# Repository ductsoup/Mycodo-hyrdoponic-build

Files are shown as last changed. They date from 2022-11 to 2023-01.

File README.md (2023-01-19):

# Mycodo-hyrdoponic-build
A straightforward example of a hardware build to run Mycodo for hydroponics.

## Overview
A few years ago we moved and I finally had the space to start messing around with indoor hydroponics to grow fresh food in winter. At first I used the Kratky method because it was cheap, easy and simple. It worked very well but had it's limitations. As things grew they required more and more tending, sometimes I didn't have the time necessary to take care of them properly. This season I wanted to move on to a more advanced ebb and flow setup that could support fruiting crops such as tomatoes.

Part of my day job is designing and building industrial control and building automation systems. Mechanical timers and checking water quality with handheld devices absolutely works but seemed a little low-tech. What I wanted was something easy to assemble with common tools that I could monitor remotely. This is what I wanted to measure and control:

- Water Quality
  - Temperature
  - pH
  - EC (electrical conductivity)
  - DO (dissolved oxygen)
- Air Quality
  - Temperature
  - Humidity
  - CO2
  - Vapor Pressure Deficit (calculated)
- Control
  - Pump 1 - Ebb and Flow (120VAC)
  - Pump 2 - Recirculation (120VAC)
  - Grow Light 1 (120VAC)
  - Grow Light 2 (120VAC)
  - Spare 120VAC or 24VDC relays

## Hardware
All sensors use the I2C bus. Additional I2C devices can be daisy chained.
- Raspberry Pi 3 or 4 (or equivalent)
  - [SanDisk 128GB Ultra microSDXC UHS-I Memory Card (or equivalent)](https://smile.amazon.com/gp/product/B08GYKNCCP/ref=ppx_yo_dt_b_asin_title_o04_s00?ie=UTF8&psc=1)
  - [2.5mm Nylon Standoffs (as needed)](https://smile.amazon.com/Generic-Spacer-Assorted-Raspberry-Pi-Standoff/dp/B014J1ZLD6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)
  - [GeeekPi 2x20 40 Pin Stacking Female Header Kit (as needed)](https://smile.amazon.com/dp/B08GC18NMK?psc=1&ref=ppx_yo2ov_dt_b_product_details)
- [Atlas/Whitebox Tentacle T3](https://atlas-scientific.com/electrical-isolation/whitebox-t3/)
  - [Atlas EZO™ pH Circuit and probe](https://atlas-scientific.com/embedded-solutions/ezo-ph-circuit)
  - [Atlas EZO™ Conductivity Circuit and probe](https://atlas-scientific.com/embedded-solutions/ezo-conductivity-circuit)
  - [Atlas EZO™ RTD Temperature Circuit and probe](https://atlas-scientific.com/embedded-solutions/ezo-rtd-temperature-circuit)
  - [Atlas EZO™ Dissolved Oxygen Circuit and probe (optional)](https://atlas-scientific.com/embedded-solutions/ezo-dissolved-oxygen-circuit/)
- [SCD41 CO2 Sensor Photoacoustic CO2, Temp & Humidity](http://adafru.it/5190)
  - [STEMMA QT / Qwiic JST SH 4-Pin Cable (modified)](https://www.adafruit.com/product/4399)
    - [Crimping Tool, housings, pins/sockets](https://www.pololu.com/product/1928)
- [Sequent Stackable 8-Channel Relay](https://smile.amazon.com/dp/B07KRKS67G?psc=1&ref=ppx_yo2ov_dt_b_product_details)
  - 120VAC/4A or 24VDC/4A 
  - [Cable Matters 2-Pack 16 AWG Heavy Duty Power Extension Cord 3 ft (modified)](https://smile.amazon.com/gp/product/B0153T1KNS/ref=ppx_yo_dt_b_asin_title_o01_s01?ie=UTF8&psc=1)
    - Wire Stripper/Cutter
  - [Wago 5-Wire Connectors](https://www.adafruit.com/product/874)

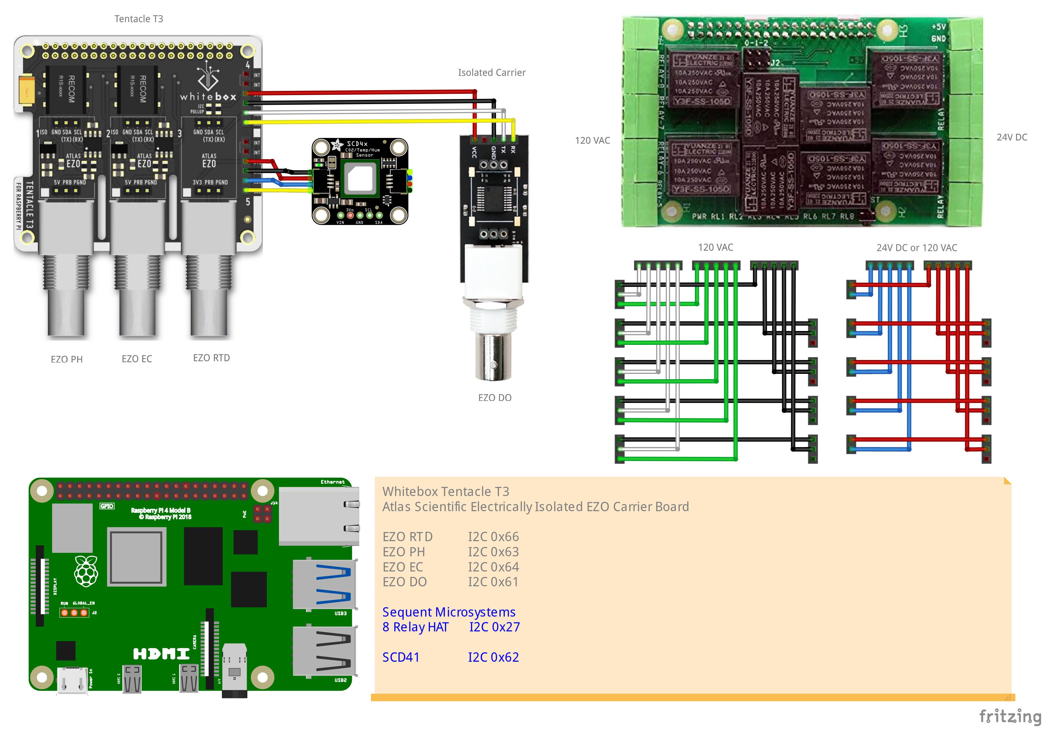
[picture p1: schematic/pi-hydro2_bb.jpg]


## Construction
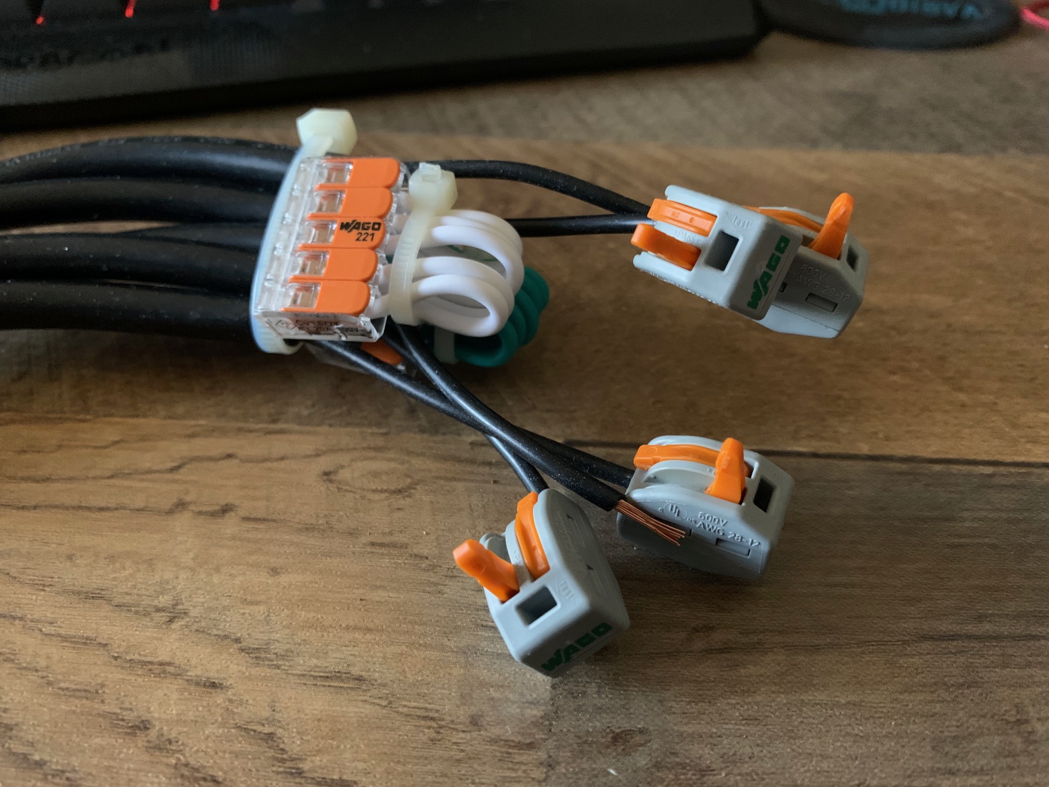
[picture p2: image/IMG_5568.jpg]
|  | For the 120VAC and 24DC use 3' (or whatever length you find convenient) extension cords with either the plug or socket removed at one end. Join using Wago connectors. Be sure to use cords and wire that can comfortably carry the load of your devices. |
| -- | :--- |
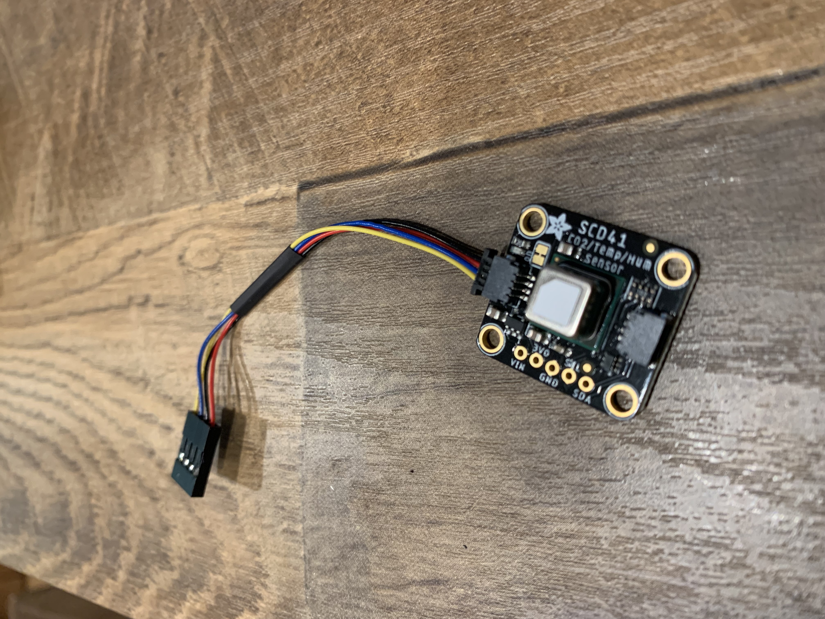
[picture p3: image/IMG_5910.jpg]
|  | The Tentacle T3 provides two spare I2C ports. To connect to SCD41 remove one end of the STEMMA QT cable and replace it with suitable 0.1" connector. Be sure to get Vin, GND, SDC and SDA in the right order. Do the same for the EZO DO board but in this case you'll make up 0.1" connections on both sides of the cable. |

## Enclosure
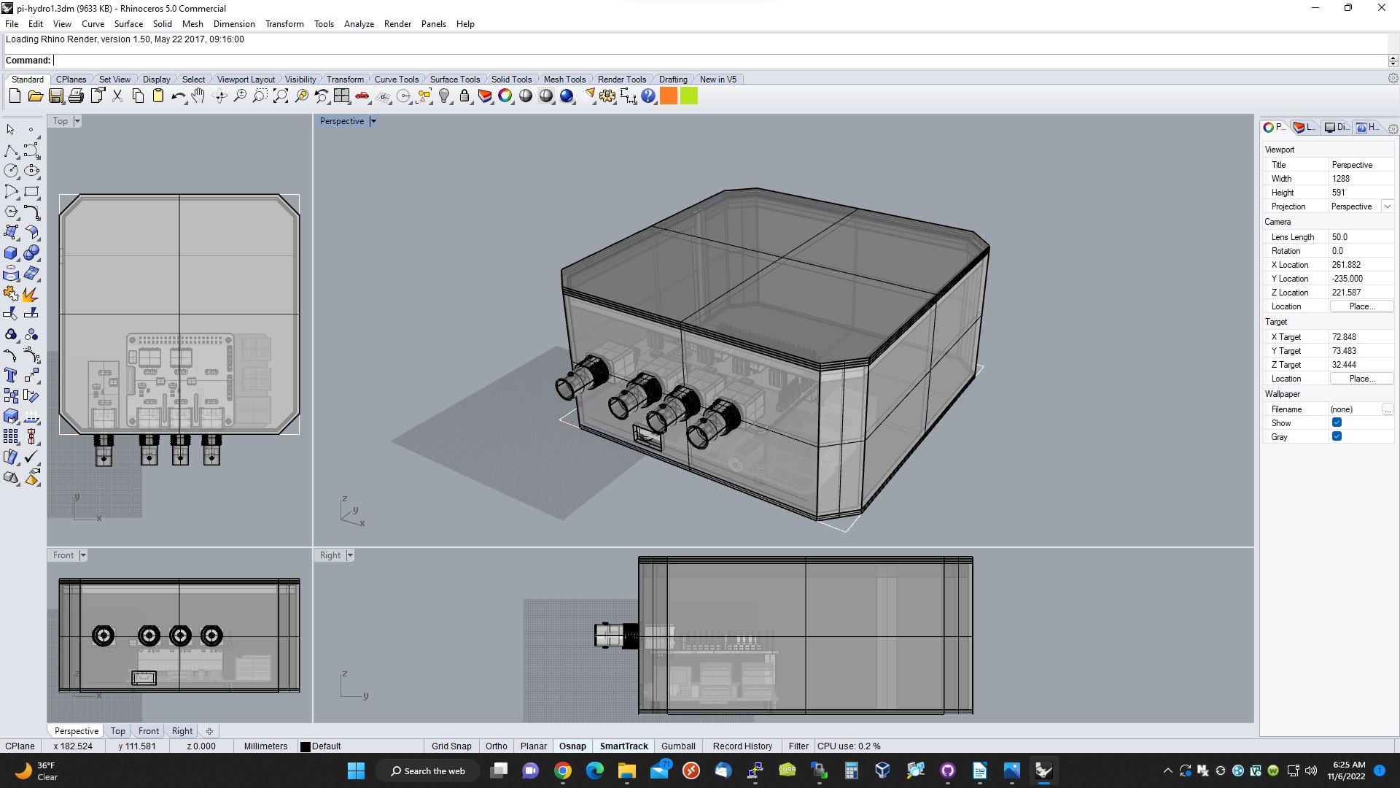
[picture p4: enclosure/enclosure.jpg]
|  | Cutouts for the BNC connectors, cords and cables require very precise measurements and special tools. Rather than modify a stock enclosure I designed and 3D printed one. Just about any material will work, I used PLA. If you're using a Pi4 or are stacking more relay boards you will have to modify the geometry. This enclosure prints on a small format Lulzbot Mini. |
| -- | :--- |

## Software
Originally I'd written my own software in Python. Then I came across [Mycodo](https://github.com/kizniche/Mycodo) which has a much nicer and more capable interface so I decided to use that instead.

Support for the Atlas and SCD41 sensors is native in Mycodo. Support for the Sequent relay board is not but fortunately there's a provision. To connect the relay board to Mycodo you'll need to install the drivers and add a shell script.

### Enable I2C
```
sudo apt update & sudo apt upgrade -y
sudo apt install -y build-essential python3-pip python3-dev python3-smbus i2c-tools
sudo raspi-config nonint do_i2c 0
sudo reboot
sudo i2cdetect -y 1

     0  1  2  3  4  5  6  7  8  9  a  b  c  d  e  f
00:                         -- -- -- -- -- -- -- -- 
10: -- -- -- -- -- -- -- -- -- -- -- -- -- -- -- -- 
20: -- -- -- -- -- -- -- 27 -- -- -- -- -- -- -- -- 
30: -- -- -- -- -- -- -- -- -- -- -- -- -- -- -- -- 
40: -- -- -- -- -- -- -- -- -- -- -- -- -- -- -- -- 
50: -- -- -- -- -- -- -- -- -- -- -- -- -- -- -- -- 
60: -- -- 62 63 64 -- 66 -- -- -- -- -- -- -- -- -- 
70: -- -- -- -- -- -- -- --  
```

### Install the Relay
```
sudo apt install git -y
# https://github.com/SequentMicrosystems/8relind-rpi/tree/main/python 
git clone https://github.com/SequentMicrosystems/8relind-rpi.git
cd 8relind-rpi/python/8relind/
sudo python3 setup.py install
cd ~/8relind-rpi/
sudo make install
8relind -h
8relind 0 test
cd ~

echo '8relind 0 write $1 $2' >script_on_off.sh
chmod +x script_on_off.sh
```
From there you can create a Shell On/Off Output in Mycodo like `/home/pi/script_on_off.sh 1 on`.

### Install the Atlas Utilities
Mycodo supports calibration for Atlas sensors. In some cases you'll want to use the Atlas utilities instead. For example, if you're using a K 0.1 or K 10 EC probe for some reason, you'll have to specify that with the Atlas utilities.
```
git clone https://github.com/AtlasScientific/Raspberry-Pi-sample-code.git
python3 Raspberry-Pi-sample-code/i2c.py
```
If you are using a Pi4 you may have problems using the Atlas utilities. A workaround for Pi 4 is [here](https://github.com/AtlasScientific/Raspberry-Pi-sample-code/issues/9).

## Gallery
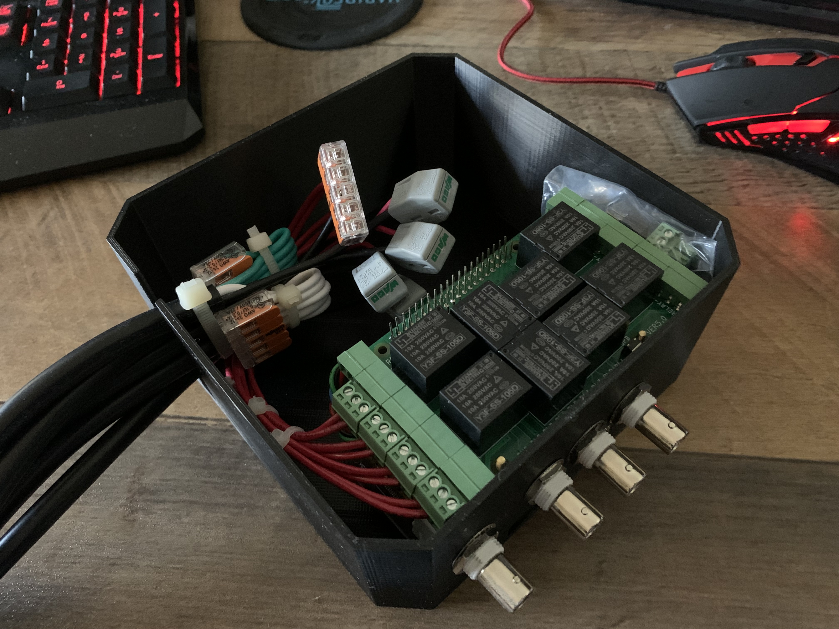
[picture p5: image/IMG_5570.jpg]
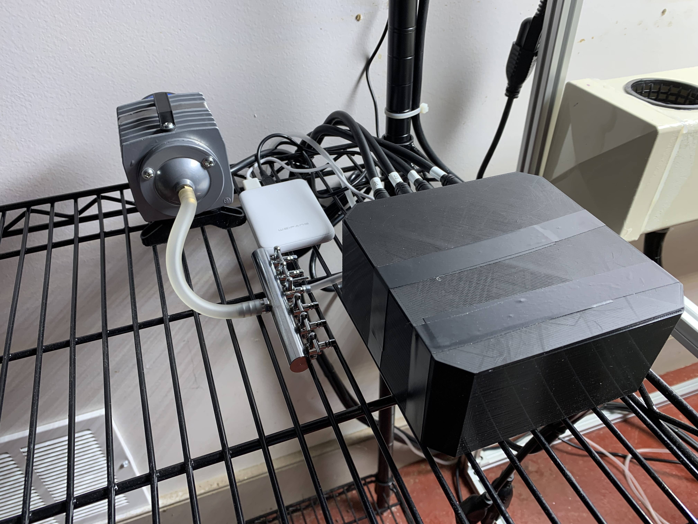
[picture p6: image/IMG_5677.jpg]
|  |   |
| --- | --- |
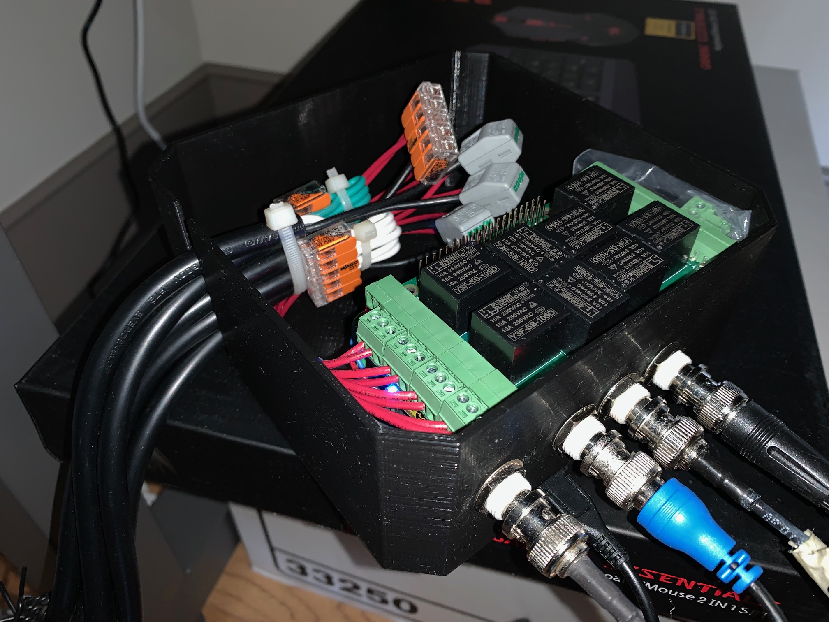
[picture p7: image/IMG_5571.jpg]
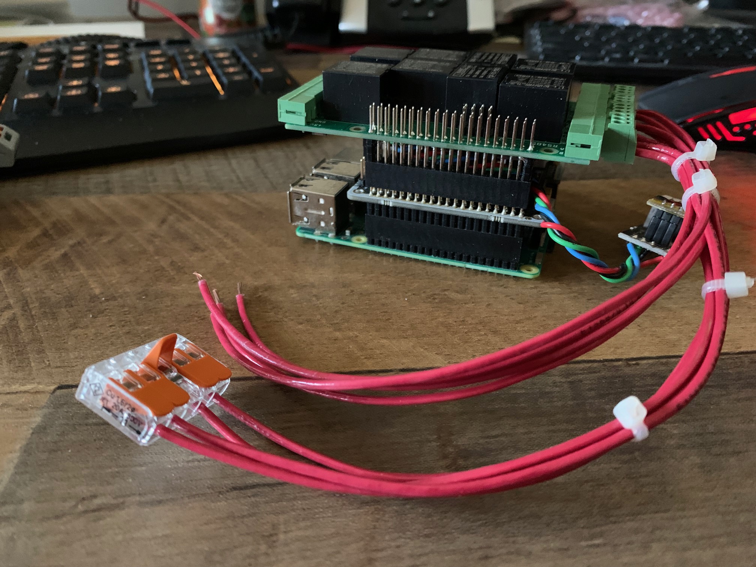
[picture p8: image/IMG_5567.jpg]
|  |  |
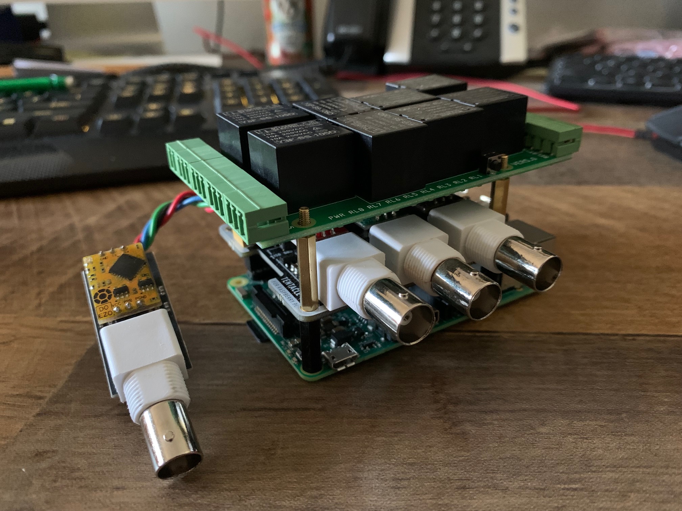
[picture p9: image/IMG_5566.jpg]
|  |  |
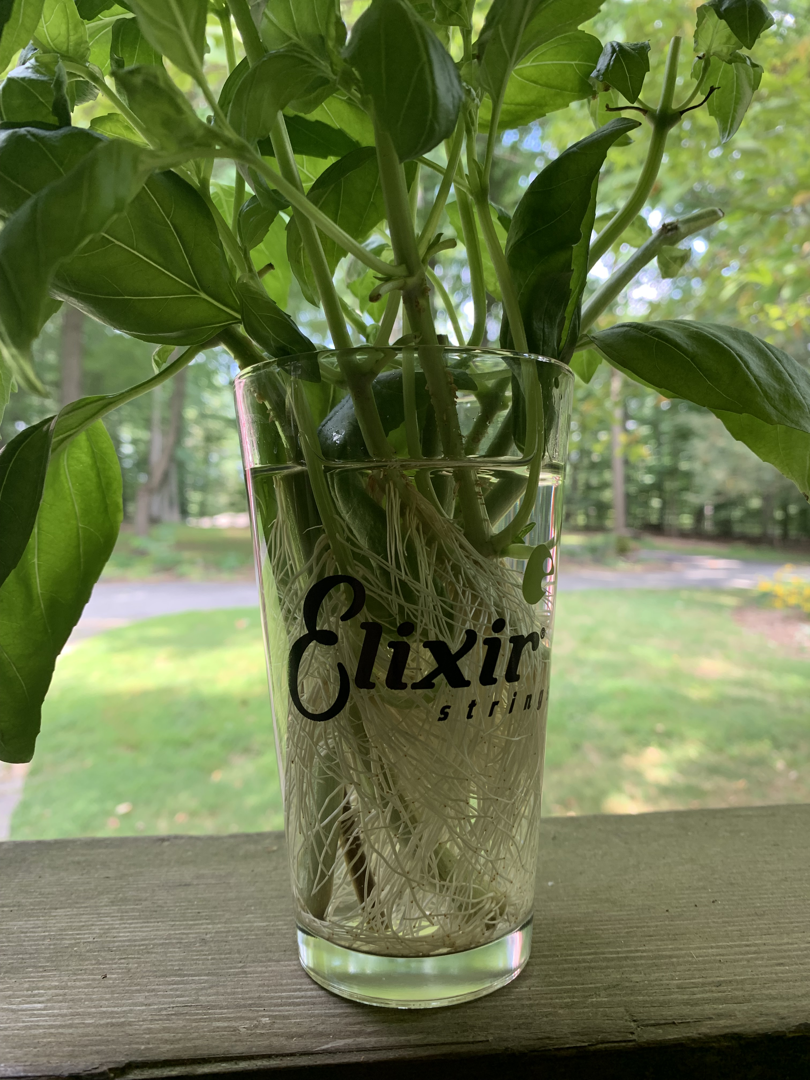
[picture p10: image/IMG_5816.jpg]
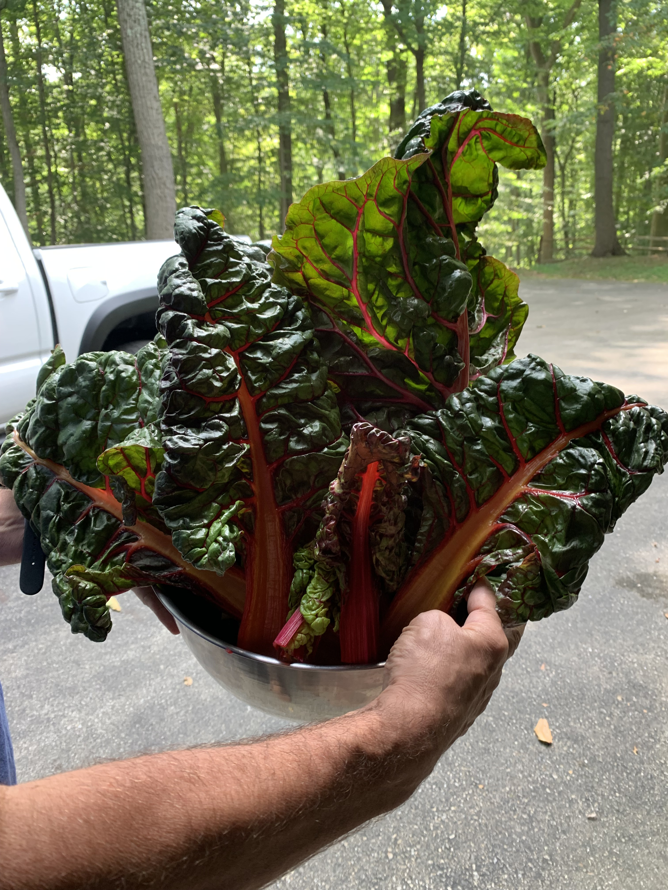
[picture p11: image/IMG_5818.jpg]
|  |  |
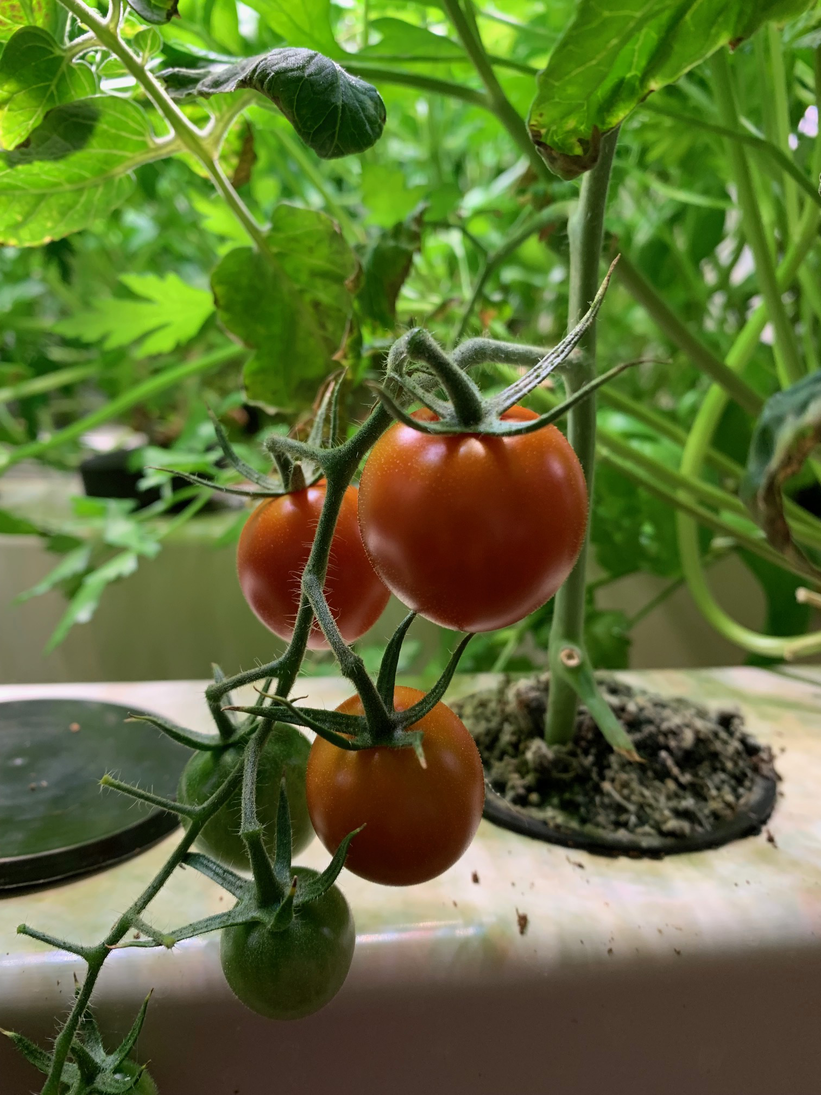
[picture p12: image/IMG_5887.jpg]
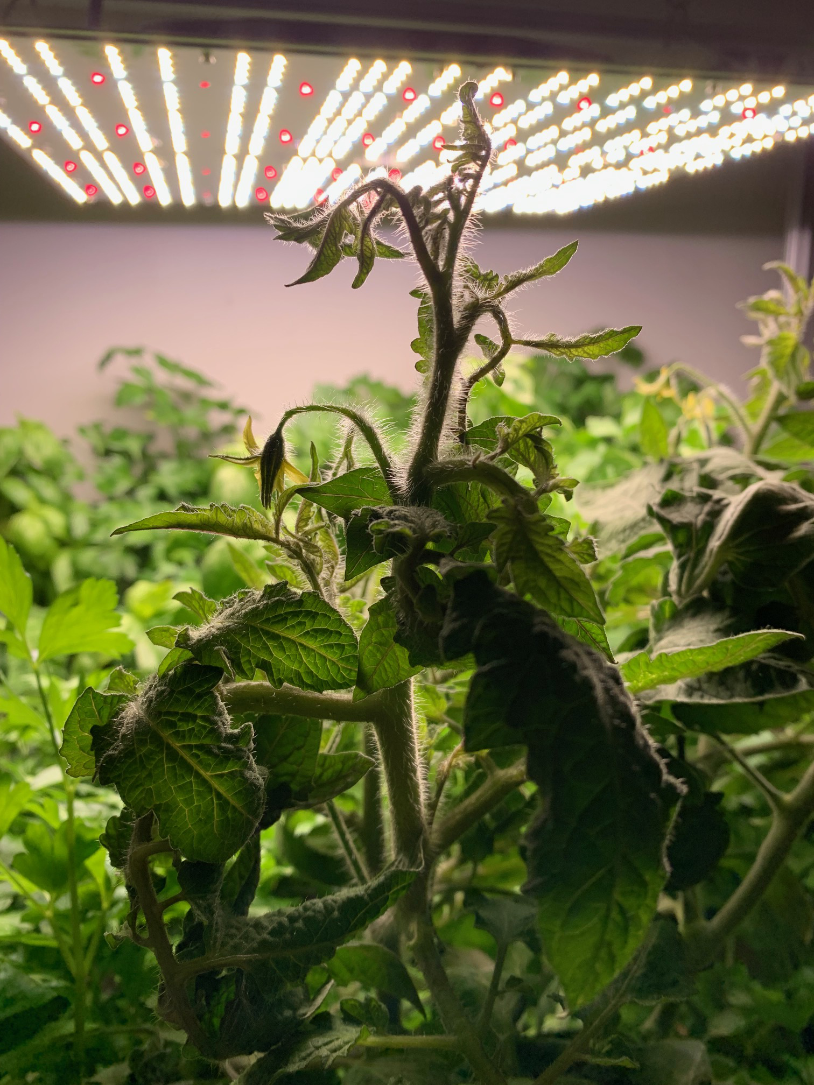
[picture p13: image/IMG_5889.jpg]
|  |  |

## Conclusion
The Pi3 works fine but it's slow. A Pi4 works much better with the caveat you need to figure a way to manage the heat it generates. Unless you're doing aquaponics the DO sensor probably isn't much use and can be elimined. The air temperature, humidity and CO2 sensor is very handy.

Just for fun I've also included a rough sketch of the frame I'm using for this system. When it came time to build that part I considered using t-slotted aluminum frames rather than a standard wire shelf from Uline. Comparing the prices for both, it was a wash so I oped for the more flexible t-slotted design. I've used extruded aluminum many times before from various vendors. Experience is Automation Direct is cheaper and faster than others.

- [Automation Direct T-Slotted Rails and Components](https://www.automationdirect.com/adc/overview/catalog/structural_frames_-z-_rails)

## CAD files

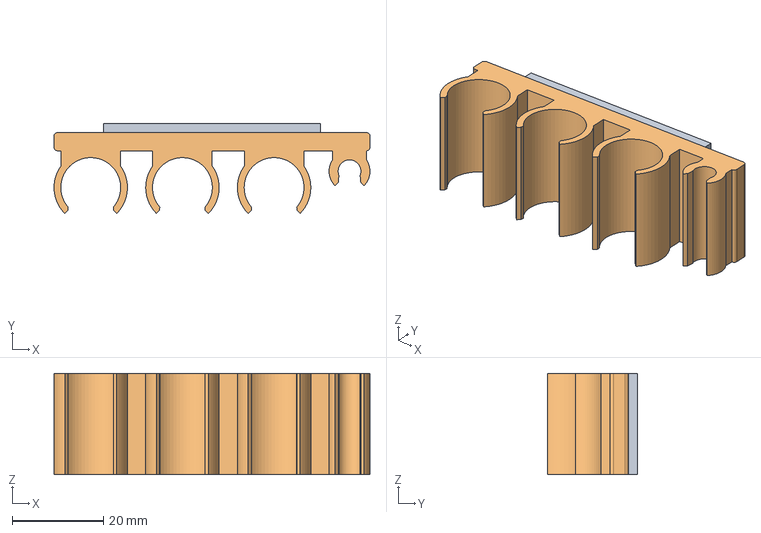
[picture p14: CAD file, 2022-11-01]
enclosure/probe_holder.stp
69.4 x 19.8 x 22.2 mm

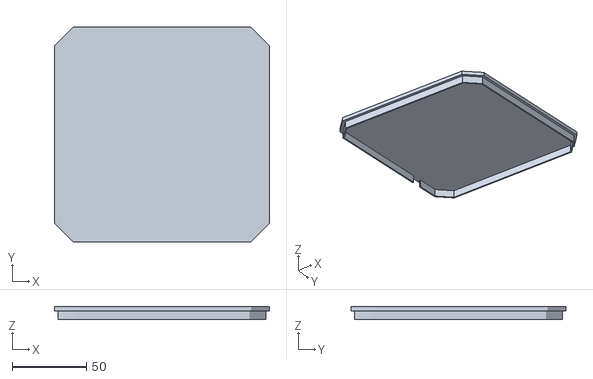
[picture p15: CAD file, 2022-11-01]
enclosure/pi-hydro1_top.stl
145.0 x 145.0 x 9.00

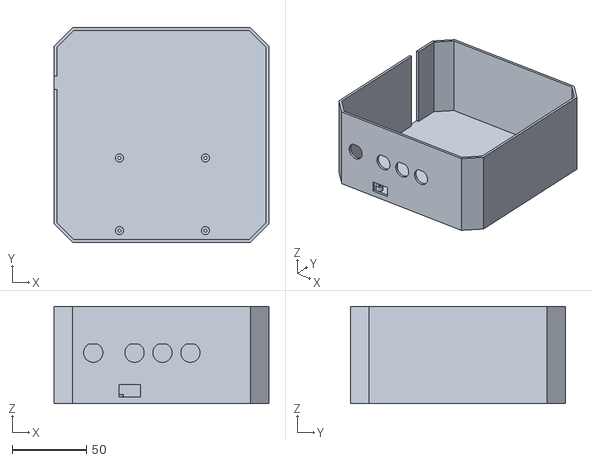
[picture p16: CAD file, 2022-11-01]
enclosure/pi-hydro1_bottom.stl
145.0 x 145.0 x 65.5

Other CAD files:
enclosure/probe_holder.3dm
enclosure/probe_holder.stl

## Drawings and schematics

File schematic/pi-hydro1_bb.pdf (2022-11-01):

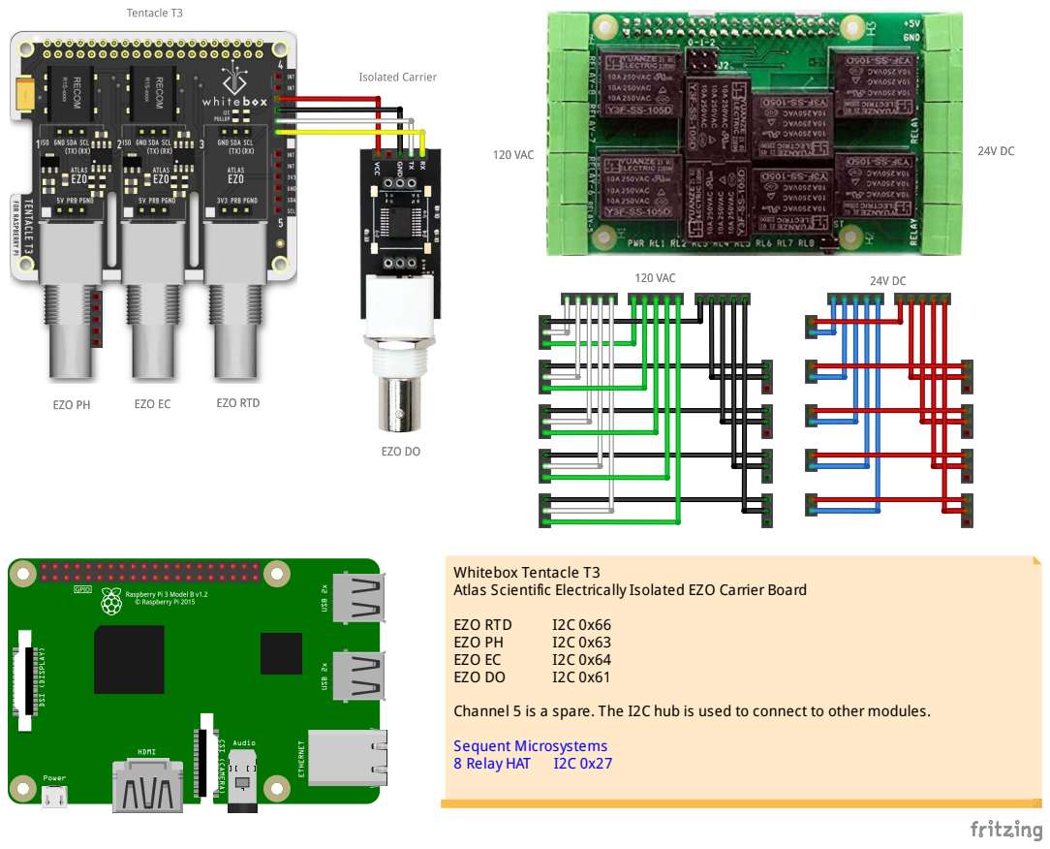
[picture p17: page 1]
EZO RTD; EZO PH; EZO EC; EZO DO; Sequent Microsystems; 8 Relay HAT

Whitebox Tentacle T3
Atlas Scientific Electrically Isolated EZO Carrier Board

Channel 5 is a spare. The I2C hub is used to connect to other modules.

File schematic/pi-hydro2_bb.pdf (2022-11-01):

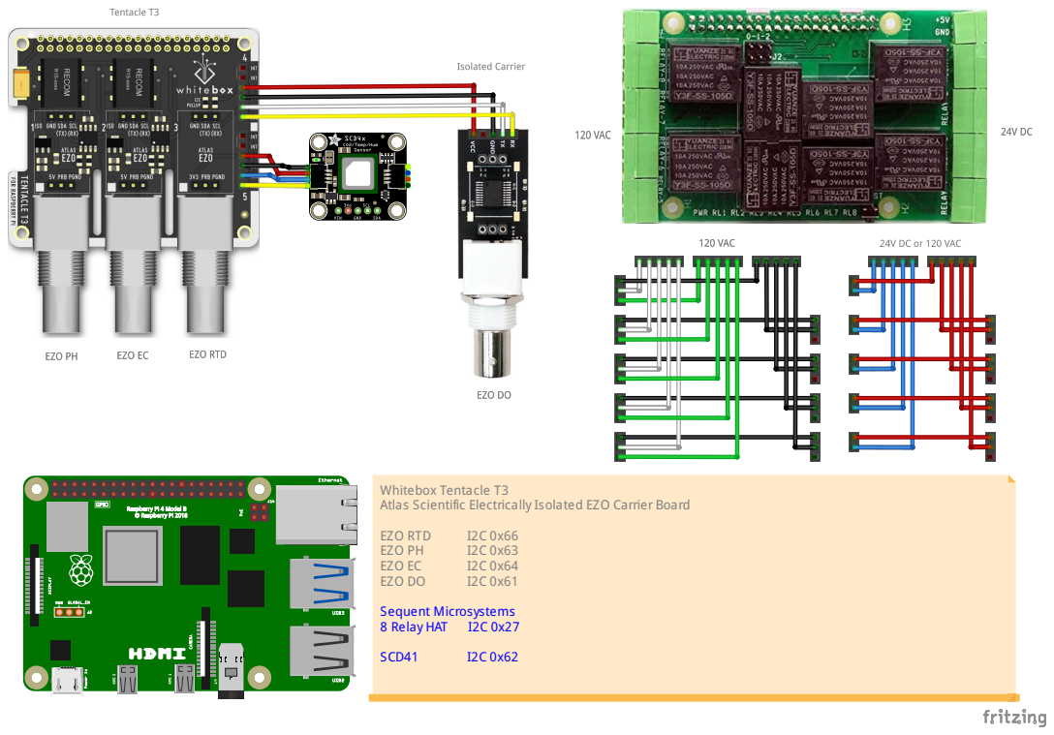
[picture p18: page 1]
EZO RTD; EZO PH; EZO EC; EZO DO; Sequent Microsystems; 8 Relay HAT; SCD41

Whitebox Tentacle T3
Atlas Scientific Electrically Isolated EZO Carrier Board
